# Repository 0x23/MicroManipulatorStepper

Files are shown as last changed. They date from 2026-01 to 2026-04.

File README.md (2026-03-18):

# Open Micro-Manipulator

This project contains an open source low-cost, easy-to-build motorized **XYZ Micro-Manipulator** motion control platform achieving submicron precision.
It's designed for applications such as optical alignment, probing electronic components, and microscopy.

Check out the YouTube video for more information about the device and how it is built:<br>
[An Open Source Motorized XYZ Micro-Manipulator - Affordable sub µm Motion Control](https://youtu.be/MgQbPdiuUTw)

<div style="display: flex; gap: 2%;">
  
  
</div>

Thanks to its parallel kinematic structure and miniature ball joints, it achieves good mechanical stiffness and a large range of motion.
The motors are off the shelf stepper motors driven by a 30 kHz closed loop controller and a very precise PWM signal.
A 'magnetic gearing' approach increases the resolution of the low-cost magnetic rotary encoders by a factor of 30 allowing for steps down to 50nm
(**Please mind the difference between resolution and accuracy**. The absolute accuracy is significantly worse.

The device can be controlled via simple G-Code commands over a USB serial interface and is thus easily integrated into other projects.
The firmware implements a complete motion planning stack with look-ahead for smooth and accurate path following capabilities.

## Getting Started

Below is a list of high level steps you can follow if you want to replicate the project. 
If you have questions or problems with the build or just want to discuss subjects related to the project, 
joint the projects community [Discord Server](https://discord.gg/maRvMVpa2Q).

1. Read this Document and watch the linked videos
2. Get the parts listed in [Bill of Materials](documentation/bom/bom.md)
3. Build the device and electronics
4. Change the hardware configuration according to your build [hw_config.h](firmware/MotionControllerRP/src/hw_config.h)
5. Upload firmware using VSCode with PlattformIO plugin
6. Calibrate axis

Also check out the setup guide for new devices: [Setup Guide](documentation/setup_guide/setup_guide.md)

## ✨NEW: Hardware Version 4.0
A new version of the hardware has been released, fixing several issues with the previous design:

- Self collision during homing fixed.
- Connection of ball joint block with screws only was not well constrained and could rotated a bit.
- No reliable way to ensure consistent linkage rod length
- Unnecessary ball joint friction
- Accurate ball position heavily dependet on print quality and corner rounding
- Rubber bands could not be changed or removed once glued in.

A video about the improved ball joint and linkage manufactoring process can be found on YouTube: [Better Ball Joints for the Open Micro-Manipulator](https://www.youtube.com/watch?v=NM2KXvRGmpg)
Also the FreeCAD model was restructured and improved and now includes all pins and fasteners. It now provides a reference for all required mechanical parts. 

<div style="display: flex;">
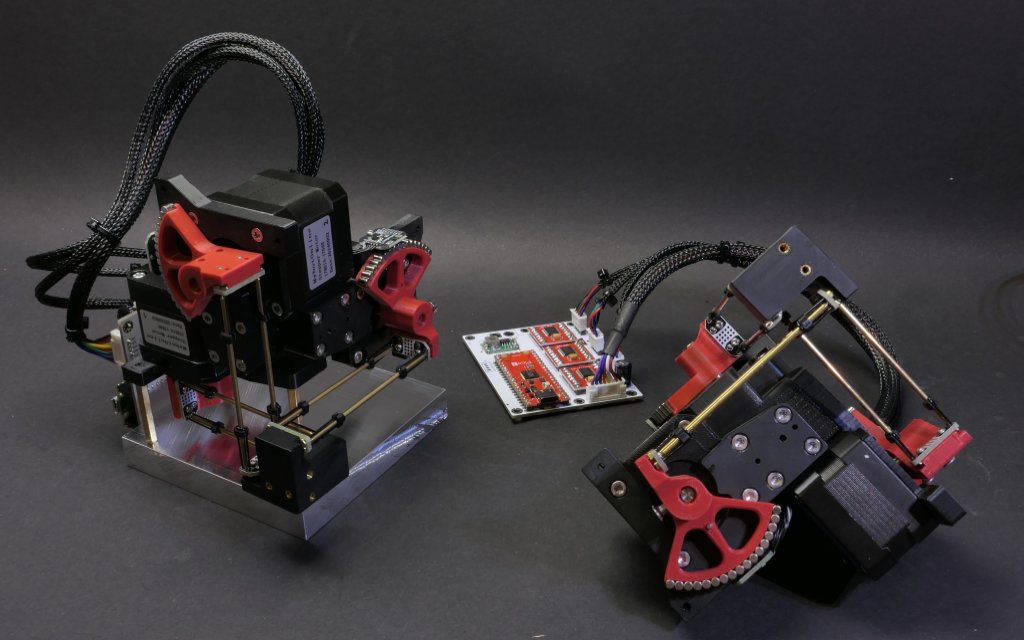
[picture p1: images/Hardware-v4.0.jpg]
    
</div>

WARNING: BOM is not updated yet...

## Open Micro-Manipulator GUI
To make testing and using the Open-Micro Manipulator easy and convenient a python control program with a graphical user interface is provided here: [Open Micro-Manipulator GUI](https://github.com/0x23/OpenMicroManipulatorGUI).
It has simple controlls to move the device around, while also displaying a live camera feed (e.g. from a microscope camera). Additional features, include a simple g-code runner and realtime mouse control (e.g. for Biology applications).

<div style="display: flex;">
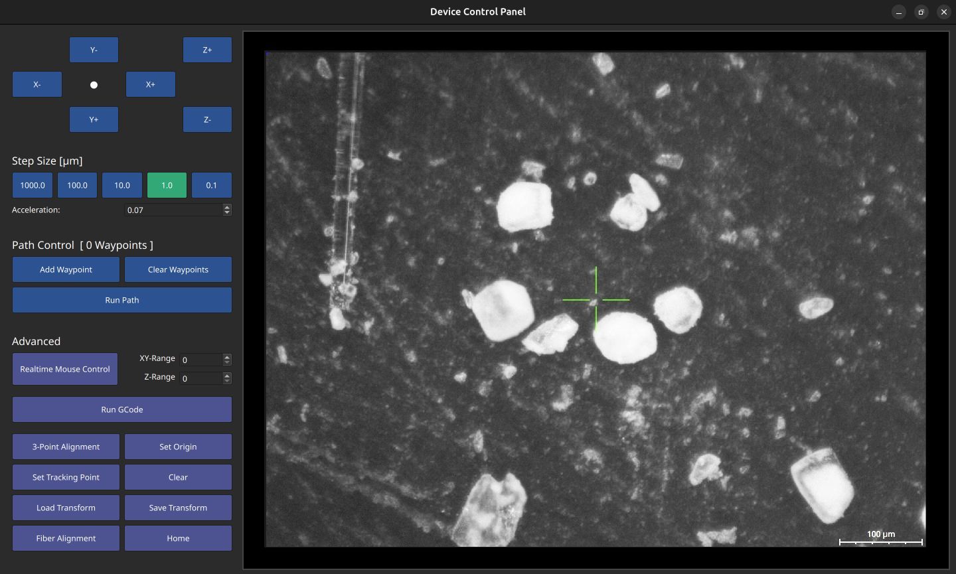
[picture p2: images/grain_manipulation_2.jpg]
    
</div>

## 🐍 Python-API

The lightweight Python API handles all serial communication and provides convenient command execution and debug message printing.
The interface includes functions to home, move, and calibrate the device, as well as to query device information.
Simply copy the [open_micro_stage_api.py](software/PythonAPI/open_micro_stage_api.py) file into your project (also install the dependencies in requirements.txt), and you’re ready to get started.

## Usage Example
```python
from open_micro_stage_api import OpenMicroStageInterface

# create interface and connect
oms = OpenMicroStageInterface(show_communication=True, show_log_messages=True)
oms.connect('/dev/ttyACM0')

# run this once to calibrate joints
# for i in range(3): oms.calibrate_joint(i, save_result=True)

# home device
oms.home()

# move to several x,y,z positions [mm]
oms.move_to(0.0, 0.0, 0.0, f=10)
oms.move_to(3.1, 4.1, 5.9, f=26)
oms.move_to(0.0001, 0.0, 0.0, f=10)

# wait for moves to finish
oms.wait_for_stop()
```

## API Functions (most relevant functions only)
```python
connect(port, baud_rate=921600)
disconnect()
set_workspace_transform(transform)
get_workspace_transform()
home(axis_list=None)
calibrate_joint(joint_index, save_result)
move_to(x, y, z, f, move_immediately, blocking, timeout)
set_tool_output(tool_idx, output_value, immediate)
set_pose(x, y, z)
dwell(time_s, blocking, timeout)
enable_motors(enable)
wait_for_stop(polling_interval_ms, disable_callbacks)
set_max_acceleration(linear_accel, angular_accel)
set_servo_parameter(pos_kp, pos_ki, vel_kp, vel_ki, vel_filter_tc)
```
## ✨ Firmware v1.0.4

Firmware 1.0.4 comes with many smaller improvements and bugfixes and a great new feature as well:

 - **Tools**: Tool usage (for example for laser engraving) is now supported on the two GPIO pins of J5 on the pcb.
              Tools are integrated into the planner and run fast and with correct timing when executing g-code.
              The tools support PWM (using the PIO feature to squeeze out extra channels without relying on software PWM).

   Example usage:
   ```
     M3 T0 S0.7  // set pwm output of tool 0 to 70%
     G4 S0.001   // dwell command (or any other motion command) - necessary to apply the tools output
   ```
   
- **Calibration**: Calibration has now some addition error checks to improve error reporting of potential problems like encoder alignment.
- **Kinematic Model Parameter**: Initialization code has been cleaned up and better comments where added to the parameters. Parameters are preset for HW v4.0 but you can toggle back to the old HW-v3.0 parameters if necessary.
- **Bugfixes**: smaller bugfixes

IMPORTANT: If you have **Hardware Version v3.0** you need to switch back to the old kinematic parameters in the [kinematic_model_delta3d.cpp](firmware/MotionControllerRP/src/kinematic_models/kinematic_model_delta3d.cpp) file (there is an #define for that at the top).

## Firmware v1.0.1

This update improves calibration, homing, logging, and adds several new G-Code commands.

### Improvements
- **Homing**: parallel homing support, higher repeatability, more accurate geometric reference  
- **Joint calibration**: refined procedure, persistent flash storage (no recalibration after reboot)  
- **Logging**: clearer and more detailed output  

### New G-Code Commands
- `G28` — Home joints (supports homing multiple axis simultanously for faster startup)
- `G24` — Set pose command (directly sets servo targets, bypassing motion controller)  
- `M17/M18` — Enable/Disable motors (with pose recovery from encoders on enable)  
- `M51` — Read encoder values  
- `M55` — Set servo loop parameters 
- `M56` — Joint calibration (with save-to-flash option)  
- `M57` — Read various information about the device state  
- `M58` — Read firmware version

## ⚙ CAD-Files

All CAD models are made in **FreeCAD** to allow everyone to view and modify the design without subscribing or paying for a proprietary CAD solution.
Note that most components are already designed with the goal to make them easily machinable on a 3-Axis CNC-Mill.
You can also 3D-Print the parts but have to live with thermal drift (carbon filled filaments can reduce this problem).

<div style="display: flex;">
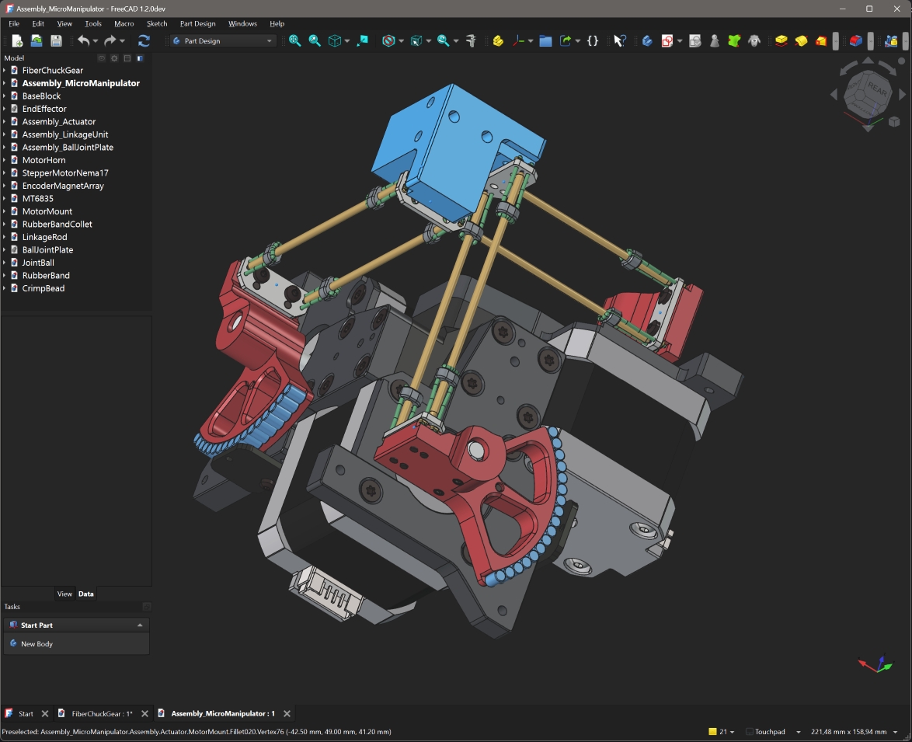
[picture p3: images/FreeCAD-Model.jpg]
FreeCAD Model
    
</div>

<br>

The CAD files can be found here: [CAD Models](construction).
Please note that FreeCAD version **1.2.0dev** was used, and the files might not work with older versions.

STL files for printing can be found here: [STL Files](construction/STL_3D_Printing/)

## ⚙ Kinematic Model

The kinematic model is defined here: [kinematic_model_delta3d.cpp](firmware/MotionControllerRP/src/kinemtaic_models/kinematic_model_delta3d.cpp).
Please check the dimensions of your build against the values set in the constructor. In particular, make sure the arm length matches.

## ⚙ Electronics

IMPORTANT: If you fabricated PCB version v1.2 (see version label on the board) you need to drill out a misplaced via on diode D1 that shorts 5V rail to ground (See [repair image](electronics/pcb_v1.2_fix.jpg) ). The problem was fixed in v1.3.

The electronics are designed in **KiCAD** and only commonly available modules (motor drivers and MCU boards) are used and connected by a simple PCB. No SMD soldering is required to populate the board to make the build extra accessible.
For usual winding resistance of your motors, the device should be powered by $${\color{lightgreen} 5V-6V }$$ (2A) to keep current and heating to a reasonable level.

<div style="display: flex; gap: 5%;">
  
  
</div>

The repository now also contains the fabrication files that can be directly uploaded to the PCB manufacturer.

## ⚙ Firmware

The firmware is written in C++ and takes some inspiration from the 'SimpleFOC' project. It aims to be streamlined and readable without any extra fuss, focusing on the hardware used in this project.
It implements path planning with look-ahead and, unlike many other motion controller projects, supports true 6DOF-Pose interpolation and planning, making it ready for driving hexapod motion platforms; that may or may not be the next step for this project.

You may find configuration for pin numbers, motor type, and other parameters in [hw_config.h](firmware/MotionControllerRP/src/hw_config.h). Please check them before uploading the firmware.

<div style="display: flex; gap: 2%;">
  
  
</div>

### Building and Flashing the Firmware

For building and flashing the firmware, Visual Studio Code (available for free on Windows and Linux) is recommended.
Install the PlatformIO add-on and open the firmware folder. You can now build and flash the firmware like any other PlatformIO project.

## ⚙ G-Code Interface

The firmware supports only a small subset of G-Code commands listed below.  
Each command is acknowledged with either an **`ok`** or **`error`** response.  

If a command provides additional information (e.g., the *get position* command), that information is returned **before** the `ok` message.  
The client must wait for an acknowledgment from the previous command before sending the next one—otherwise, behavior is undefined.
| Command | Description |
|---|---|
| `G0 X Y Z F` | Move the end-effector in a straight line to the specified position. <br>• `X`, `Y`, `Z`: target positions <br>• `F`: feed rate |
| `G1 X Y Z F` | Same as `G0`. |
| `G4 S/P` | Dwell/pause for a specified time. <br>• `S`: seconds <br>• `P`: milliseconds |
| `G24 X Y Z A B C` | Directly set current pose for servo loops with optional rotation vector* `A`, `B`, `C`. |
| `G28 A-F` | Home one or more joints. <br>• Optional joint selection `A`–`F`. |
| `M3` | Set Tool output. <br>• `T`: tool index <br>• `S`: output value (0.0..1.0) <br> Note: new values is only applied on the next motion or dwell command |
| `M17` | Enable motors and read current pose as the start pose. |
| `M18` | Disable motors. |
| `M50` | Get current internal pose. (Encoders are not read here) |
| `M51` | Get current encoder angles (in degrees) and raw encoder values. |
| `M52` | Get the number of items in the planner queue. |
| `M53` | Check if all planned moves are finished (`1` = finished, `0` = not finished). |
| `M55 A B C D F` | Set servo loop parameters. <br>• `A`, `B`: position PI controller gains (P and I) <br>• `C`, `D`: velocity PI controller gains (P and I) <br>• `F`: velocity filter time constant |
| `M56 J S` | Calibrate a joint. <br>• `J`: joint index <br>• `S`: save calibration result |
| `M57` | Get device and servo loop info: homing/calibration state, angles, loop frequencies, and file list. |
| `M58` | Get firmware version. |
| `M204 L A` | Set linear and angular acceleration. <br>• `L`: linear acceleration <br>• `A`: angular acceleration |

*Note: The communication protocol uses 3D vectors for rotations. The direction represents the rotation axis and the length of the vector represents the angle of rotation around the axis.

## ❤️ Support

If you'd like to support this project, consider the following:

- **Contribute to the build guide** – Help improve or expand the build instructions by submitting pull requests or opening issues with suggestions.
- **Characterize typical radial stepper motor shaft error motion** – Measure radial error motion of the shaft of multiple Nema-17 stepper motors (see Cylos Garage for more information about the subject: https://www.youtube.com/watch?v=gt2gK-oxy5s).
- **Give feedback on the build experience** – Let us know what worked, what didn’t, and how the process could be smoother for others.
- **Support the project on Ko-fi** – If you find this project valuable, you can support it financially via [Ko-fi](https://ko-fi.com/diffractionlimited) ☕.

## Youtube Video
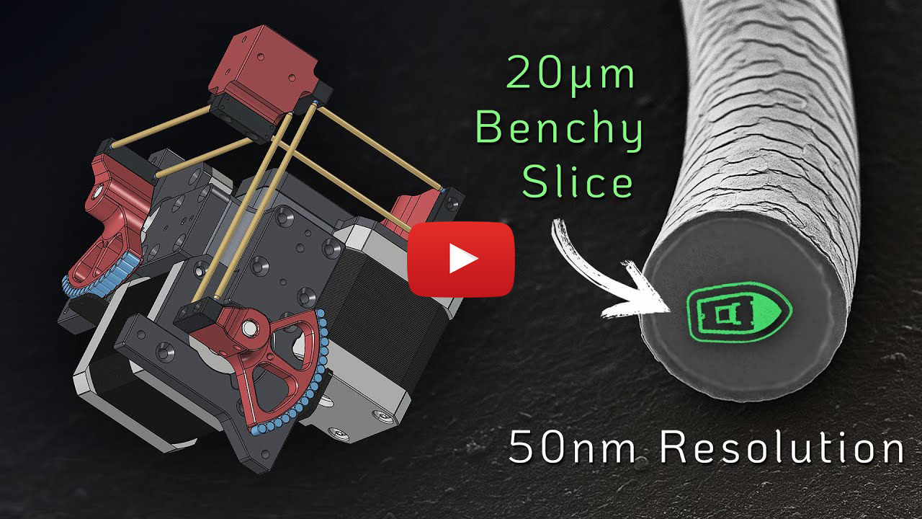
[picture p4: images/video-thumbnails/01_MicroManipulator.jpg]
Watch the video (https://youtu.be/MgQbPdiuUTw)

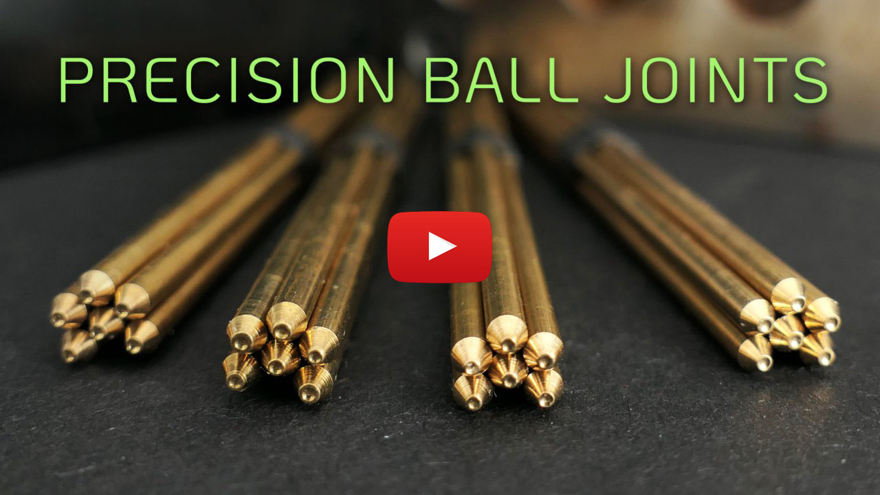
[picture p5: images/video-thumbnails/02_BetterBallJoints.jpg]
Better Ball Joints for the Open Micro-Manipulator (https://youtu.be/MgQbPdiuUTw)


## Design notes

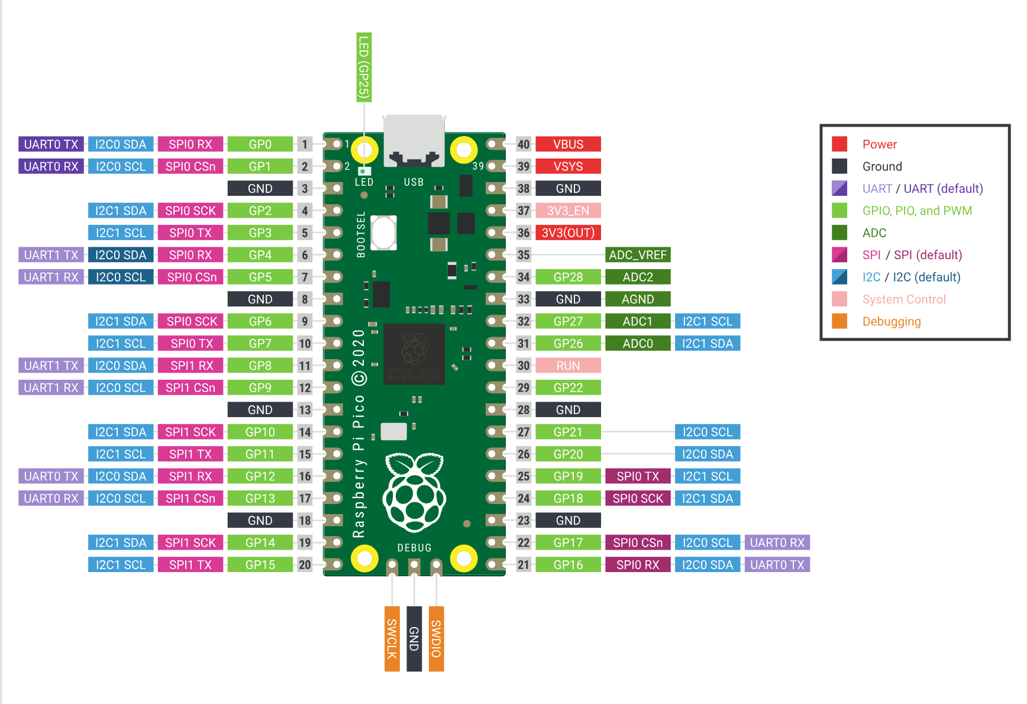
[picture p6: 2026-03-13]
firmware/MotionControllerRP/Rp2350-Pico_Pinout.png

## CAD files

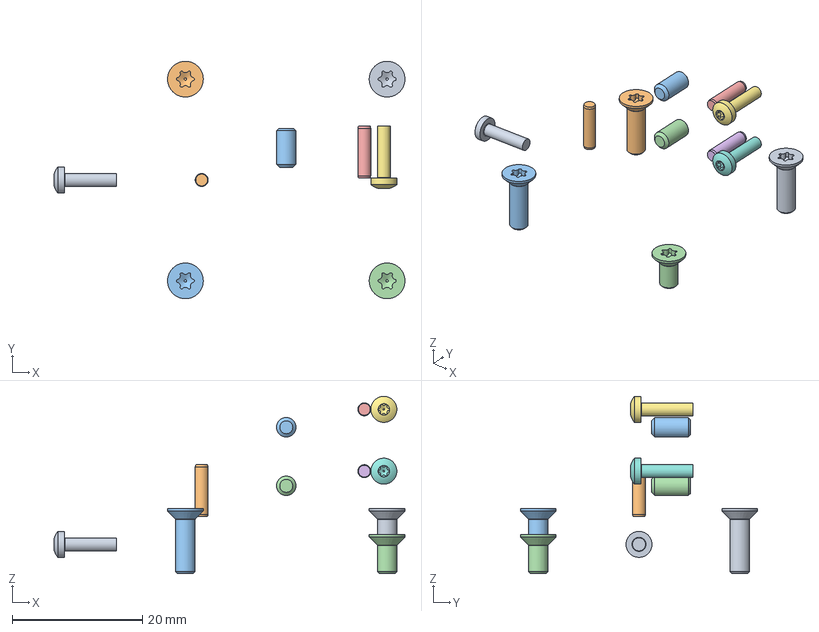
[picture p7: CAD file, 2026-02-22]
construction/micro_manipulator/Assembly_Actuator.FCStd
53.9 x 36.5 x 27.2 mm
M3x10-Screw x 2
M3x10-Screw008 x 2
M3x10-Screw009 x 2
M3x6-Screw x 2
2 mmx8-Pin x 2
2 mmx8-Pin012 x 2
M2x8-Screw x 2
M2x8-Screw009 x 2
M2x8-Screw004 x 2
2 mmx8-Pin011 x 2
M3x6-Screw003 x 2
M3x6-Screw004 x 2

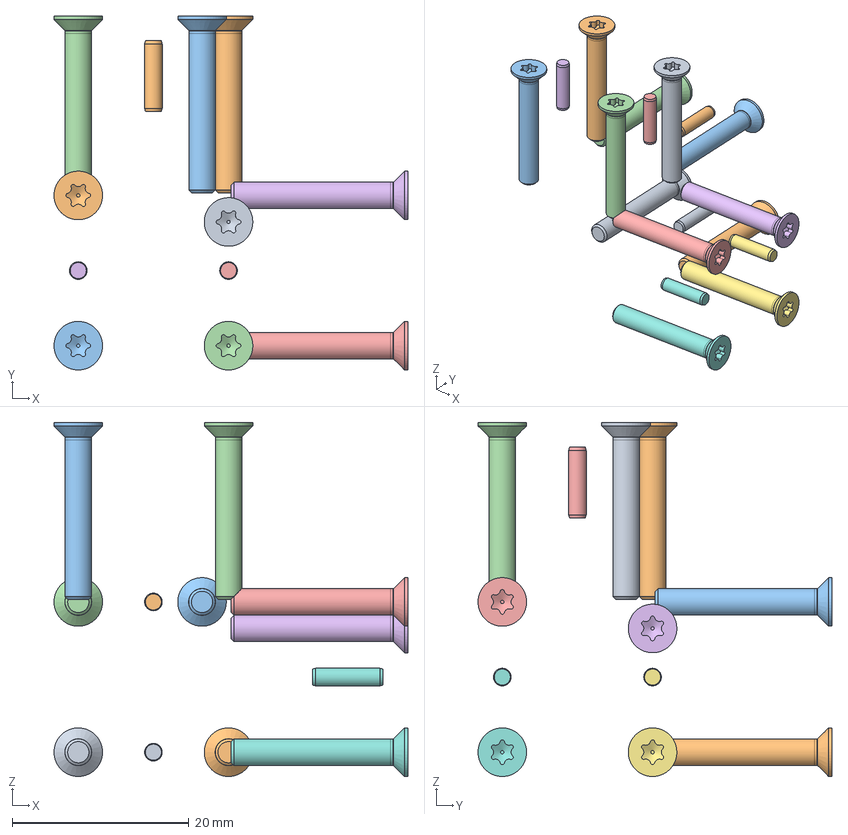
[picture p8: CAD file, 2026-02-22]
construction/micro_manipulator/Assembly_MicroManipulator.FCStd
40.0 x 40.0 x 40.0 mm
M3x20-Screw x 2
M3x20-Screw281 x 2
M3x20-Screw282 x 2
M3x20-Screw283 x 2
M3x20-Screw277 x 2
M3x20-Screw278 x 2
M3x20-Screw279 x 2
M3x20-Screw280 x 2
M3x20-Screw262 x 2
M3x20-Screw263 x 2
M3x20-Screw264 x 2
M3x20-Screw265 x 2
2 mmx8-Pin027 x 2
2 mmx8-Pin028 x 2
2 mmx8-Pin029 x 2
2 mmx8-Pin030 x 2
2 mmx8-Pin031 x 2
2 mmx8-Pin032 x 2

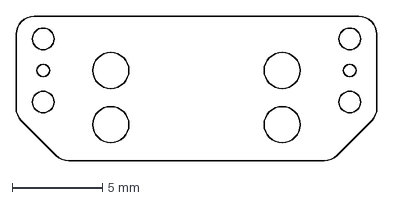
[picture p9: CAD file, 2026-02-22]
construction/micro_manipulator/balljoint_plate_pcb/BallJointPlate-Contour.dxf
20.0 x 8.00 mm

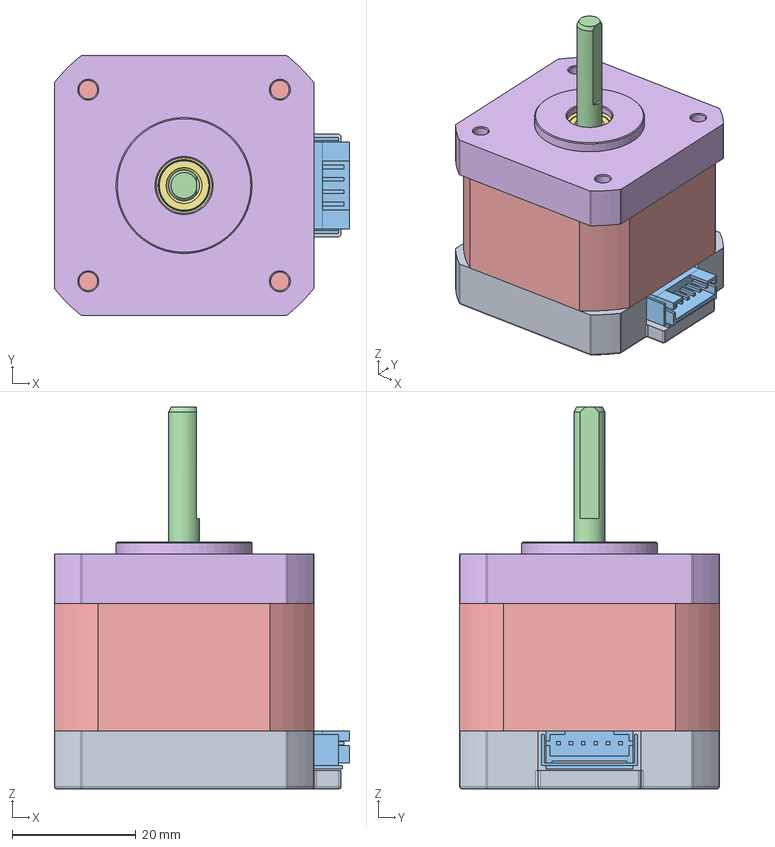
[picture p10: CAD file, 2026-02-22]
construction/micro_manipulator/StepperMotorNema17.FCStd
47.8 x 42.0 x 61.8 mm
rear end cap
rear bearing
connector
shaft
stator
front end cap
front bearing
M3x10-Screw
M3x10-Screw004
M3x10-Screw005
M3x10-Screw006

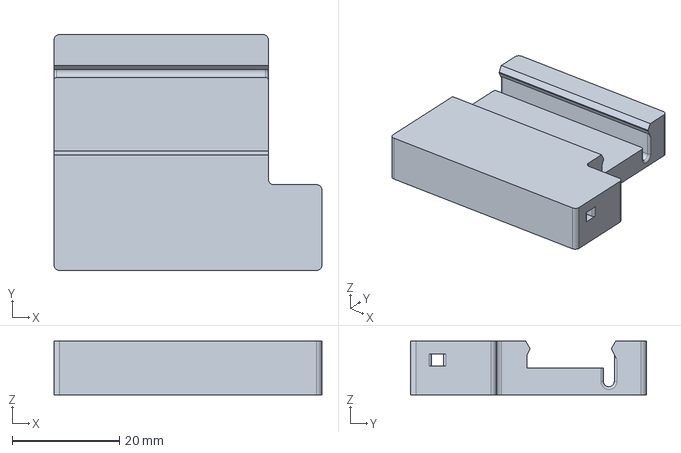
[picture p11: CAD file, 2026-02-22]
construction/tools/rod_embossing_tools/rod_lenth_setting_press/rod_guide.FCStd
50.0 x 44.0 x 10.0 mm

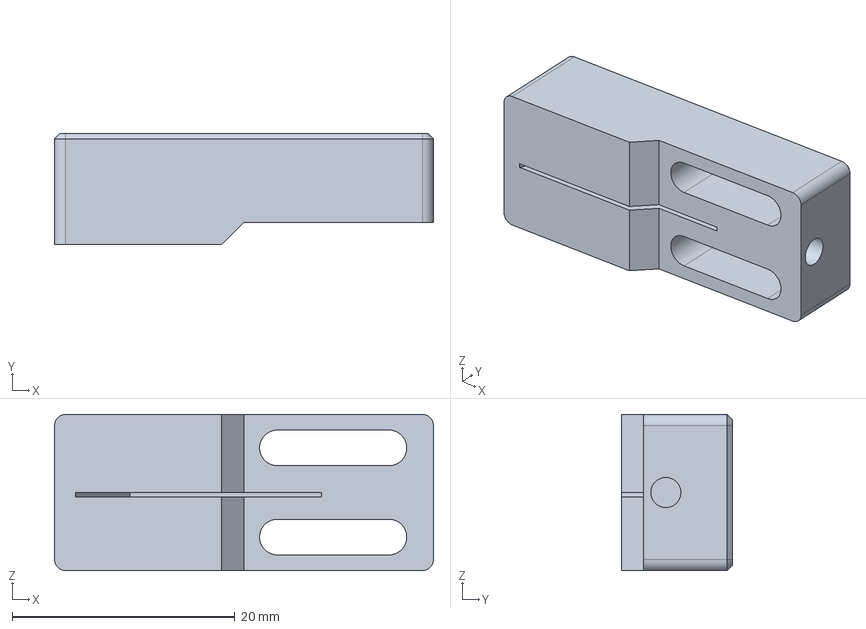
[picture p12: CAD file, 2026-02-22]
construction/tools/rod_embossing_tools/rod_sharper/BladeCarrier.FCStd
34.0 x 10.0 x 14.0 mm

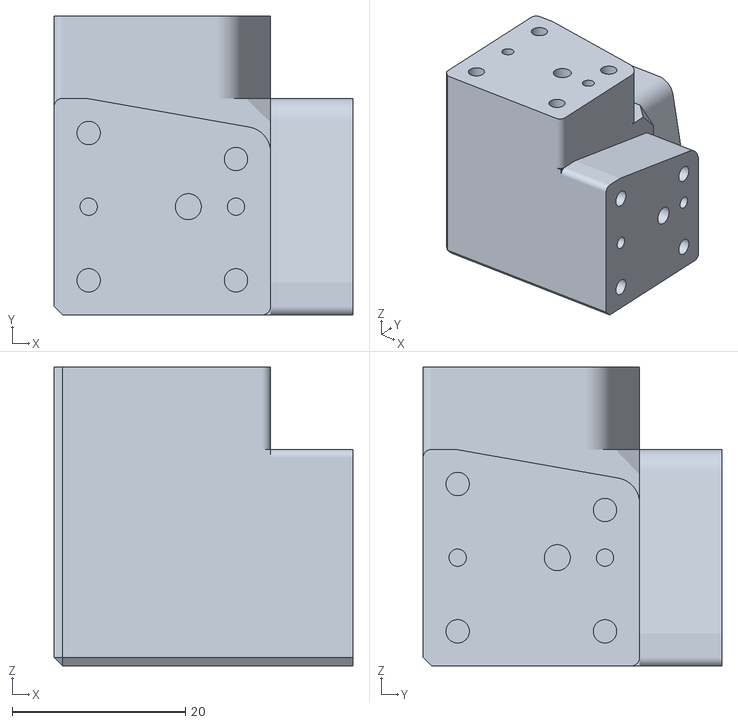
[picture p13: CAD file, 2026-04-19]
construction/v4_3dprinting_stl/machine/BaseBlock.stl
34.5 x 34.5 x 34.5

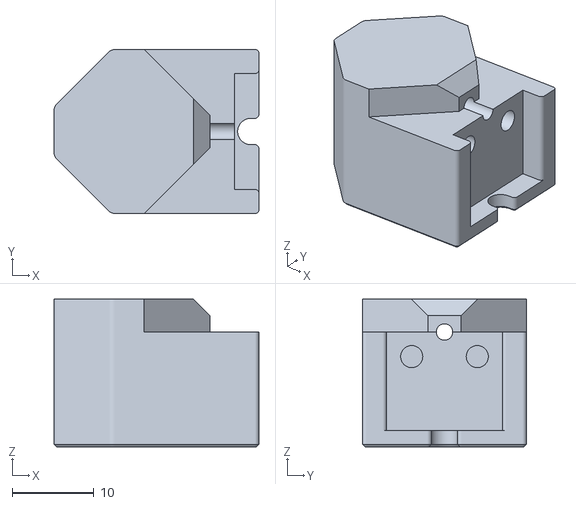
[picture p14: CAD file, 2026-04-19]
construction/v4_3dprinting_stl/tools/rod_sharpener/RodGuide.stl
25.0 x 20.0 x 18.0

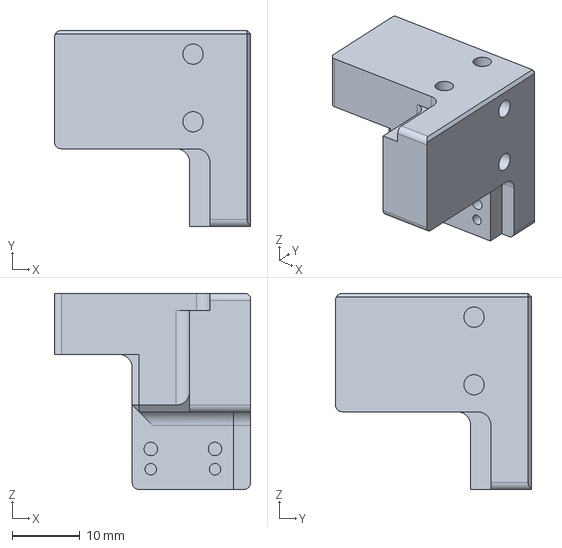
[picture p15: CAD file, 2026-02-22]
construction/micro_manipulator/EndEffector.FCStd
29.0 x 29.0 x 29.0 mm

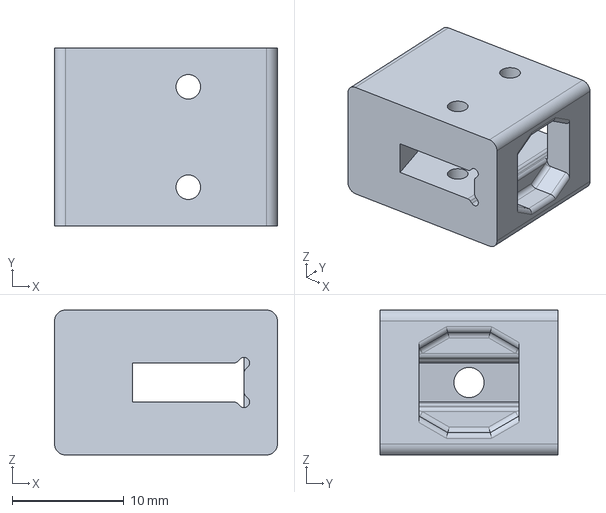
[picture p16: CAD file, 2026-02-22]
construction/tools/rod_embossing_tools/rod_lenth_setting_press/caliper_clamp.FCStd
20.0 x 16.0 x 13.0 mm

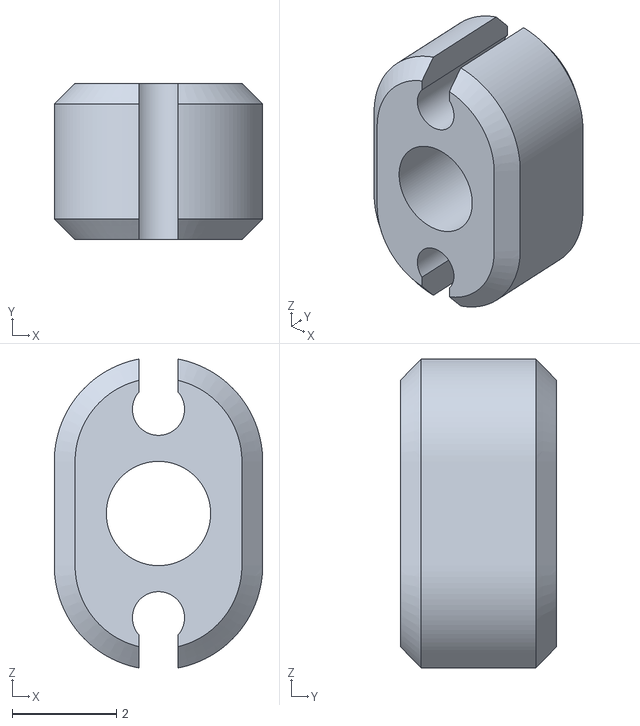
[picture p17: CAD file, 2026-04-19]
construction/v4_3dprinting_stl/machine/RubberBandCollet.stl
4.00 x 3.00 x 5.93

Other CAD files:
construction/micro_manipulator/Assembly_EndEffector.FCStd
construction/micro_manipulator/Assembly_BallJointPlate.FCStd
construction/micro_manipulator/Assembly_LinkageUnit.FCStd
construction/v4_3dprinting_stl/tools/rod_length_setting_press/RodGuide.stl
construction/tools/rod_embossing_tools/rod_sharper/RodGuide.FCStd
construction/v4_3dprinting_stl/tools/rod_length_setting_press/CaliperClamp.stl
construction/v4_3dprinting_stl/tools/rod_sharpener/BladeCarrier.stl
construction/micro_manipulator/BallJointPlate.FCStd
construction/micro_manipulator/BaseBlock.FCStd
construction/micro_manipulator/CrimpBead.FCStd
construction/micro_manipulator/EncoderMagnet.FCStd
construction/micro_manipulator/EncoderMagnetArray.FCStd
construction/micro_manipulator/JointBall.FCStd
construction/micro_manipulator/LinkageRod.FCStd
construction/micro_manipulator/MT6835.FCStd
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

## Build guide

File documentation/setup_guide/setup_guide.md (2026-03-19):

# Setup Guide

This guide walks you through the setup of your new **Open Micro-Manipulator** device.

## Checklist for New Devices

1. **Was the mechanical limit pin added to the rotor?**  
   This pin is required for proper homing of the device.

    <div style="display: flex;">
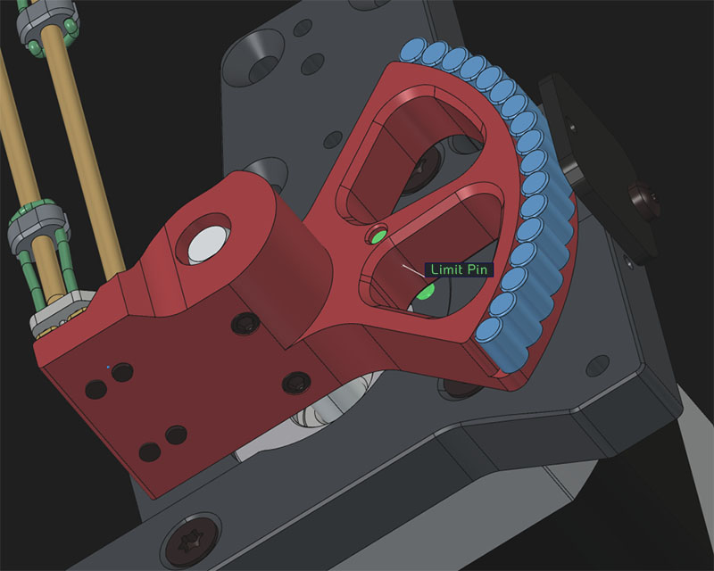
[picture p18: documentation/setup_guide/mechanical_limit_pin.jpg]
Mechanical Limit Pin
        
    </div>

2. **Are the screws that secure the rotor to the motor shaft installed?**  
   If the rotor is not firmly attached, it may slip imperceptibly during homing or other movements, leading to problems during calibration and homing.

3. **Is the homing direction correct?**  
   During the homing command (`G28`), the end effector should move toward the base.  
   If it moves in the opposite direction, rewire the motor to reverse its direction.

   <div style="display: flex;">
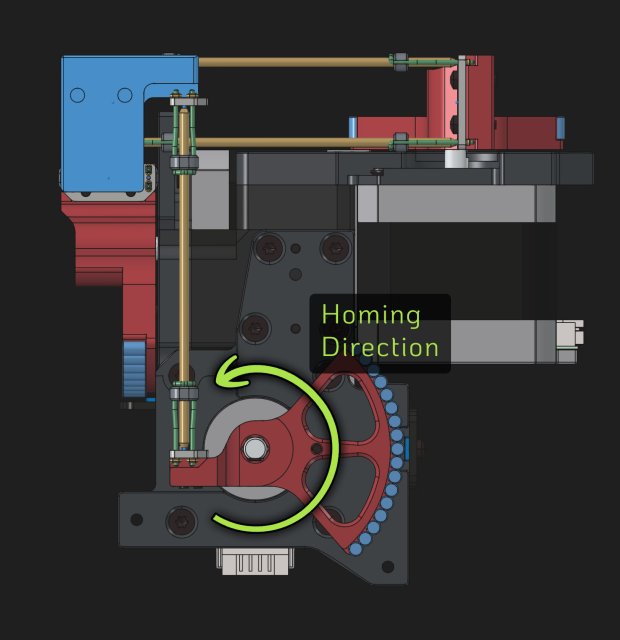
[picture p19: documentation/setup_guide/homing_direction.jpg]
       
   </div>

## Calibration and Checking the Encoders

You can use the calibration plotter to check if your encoders are working as expected.
On the left you see a good calibration on the right a bad calibration.

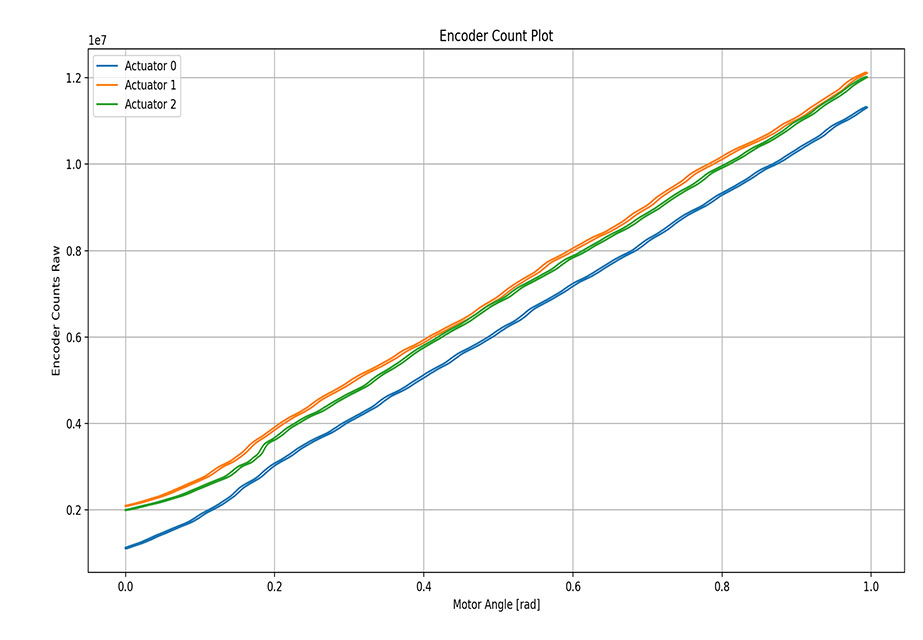
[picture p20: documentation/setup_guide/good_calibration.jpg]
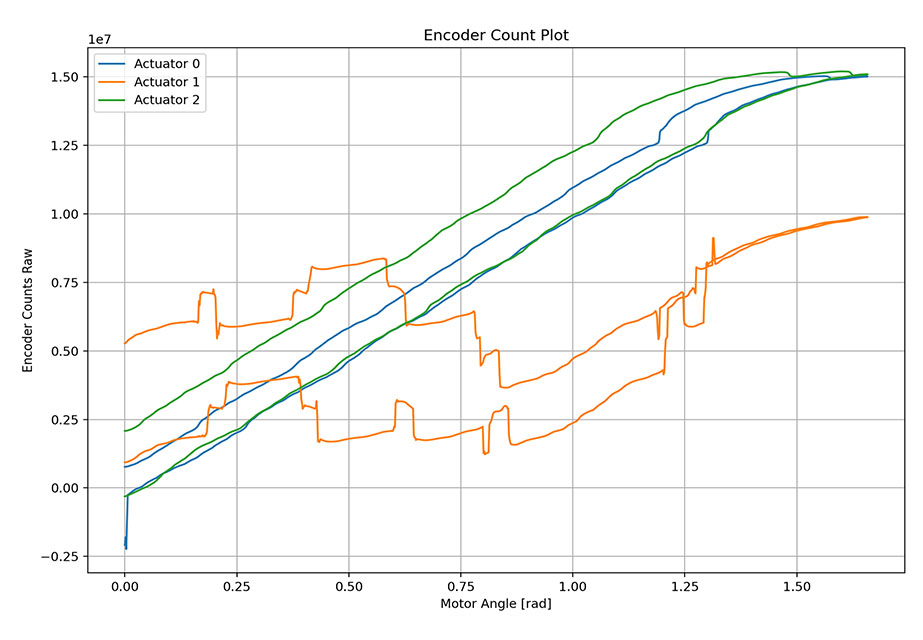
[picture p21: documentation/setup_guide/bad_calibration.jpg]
|  |  |
:--:|:--:
| **Good calibration** | **Bad calibration** |

THIS DOCUMENT IS UNFINISHED AND WORK IN PROGRESS...

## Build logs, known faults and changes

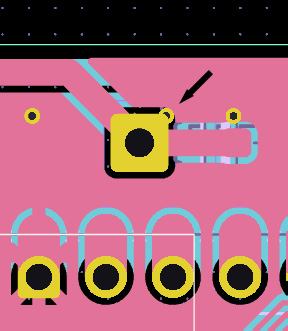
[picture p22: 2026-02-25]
electronics/control_board/pcb_v1.2_fix.jpg

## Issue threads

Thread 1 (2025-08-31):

Link the YouTube video in the README

gdevenyi, 2025-08-31:
Currently it's missing

https://youtu.be/MgQbPdiuUTw

Closed 2025-09-01.

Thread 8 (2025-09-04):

Questions about BOM file (Encoder qty, steel ball size, stepper motor spec)

Jonas-Meyer97, 2025-09-04:
Hello,

I have a few questions regarding the BOM file:

- The MT6835 Magnetic Encoder Module is listed with a quantity of 4, but from the design it seems only 3 are required. Could you confirm the correct number?
- The steel ball is noted as 1.25 mm diameter, but the CAD files and video reference 1.5 mm. Which size should be used?
- For the Nema 17 stepper motor, should we use the 1.8° or 0.9° variant?

Thanks for clarifying!

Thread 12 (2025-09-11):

Short to GND on diode output.

Dainius-G, 2025-09-11:
Short to GND on diode output.

0x23, 2025-09-13:
PCB layout is corrected.

Closed 2025-09-13.

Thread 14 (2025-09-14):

chore(electronics): add .gitignore

gustavo-alberto, 2025-09-14:
### Description
The `electronics` module currently does not have a `.gitignore` file.
This causes unnecessary temporary files to be tracked in version control.

### Proposed solution
- Add a `.gitignore` file to the `electronics` module.

### Benefits
- Keeps the repository clean.
- Prevents accidental commits of temporary files.
- Improves collaboration by reducing noise in pull requests.

Closed 2025-09-14.

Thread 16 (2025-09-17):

Assembly instructions / WireMountfixture ?

11mbs, 2025-09-17:
Hi,
Thank you so much for the amazing project!
It's so beautifully designed and I'm really excited to build one. :D

Just before  all the parts have arrived, I was looking around and came up with a few questions about assembly:
1. Is there any use for the Wire Mount Fixture model, or is it left over from the previous project / versions?

2. How long to make the loops of the PU rubber band?
The video shows 50mm lengths being cut, but the length of the loop doesn't match this after trimming.

3. I notice the BOM here says 1.25mm steel balls, but the video says 1.5mm - are both usable?

Thanks again for all the work you've put in here, it's really really cool!

JamesNewton, 2025-09-17:
Jumping in to help where I can. Your question 3 has been answered before: The size isn't critical.

0x23, 2025-09-18:
1. Its a leftover and I removed it from the repo, thanks for pointing that out
2. The total length of rubberband in the loop (not counting the length within the holes)  is about 20mm
3. Both work - I will probably go down to 1mm in future with the upcoming ball joint improvement
4. I use a pressfit and it works so far (but not ideal with 3d-printed parts). I recommend a drop of CA-Glue
5. Yes (CA-Gue as well). I plan to use screws in future but I am not there yet with the design.
6. There are three mounting 3 holes in the motor plate. I temporary mounted my device with 3d printed spacers to a steel plate:

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

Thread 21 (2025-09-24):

FreeCAD blog post and FOSDEM

concretedog, 2025-09-24:
Hi, I'm Jo and I write some content for the official FreeCAD news blog and I've just drafted a post on this amazing project. It's probably scheduled for publishing tomorrow or Friday. I'm just wondering though were you are in the world and if by any chance you were planning to attend FOSDEM next year? FreeCAD and KiCad have a joint booth each year and this would be an amazing project to have on the booth desk showcasing both FreeCAD and KiCad. Obviously unlikely this can happen, but it's always worth asking!

concretedog, 2025-09-25:
The post is now live on the [FreeCAD blog](https://blog.freecad.org/2025/09/25/forged-in-freecad-xyz-micro-manipulator-for-sub-micron-motion-control/).

0x23, 2025-09-26:
FOSDEM is in Brussels right? Its actually not too far away. Can you contact me via email ?

concretedog, 2025-09-26:
Yes Brussels, 31st January 1st Feb 2026. https://fosdem.org/2026/

concretedog, 2025-09-26:
Just emailed you on the email in your recent commits. Maybe check spam etc. Be great if we can work this out!

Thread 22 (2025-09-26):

Discord

Dainius-G, 2025-09-26:
Hi

Thank you for sharing such an interesting project! I’m currently in the middle of building the MicroManipulatorStepper and really enjoying it.

From what I’ve seen, most of the project’s presence is on YouTube and GitHub. Those are great for publishing updates and source code, but they don’t provide an easy space for builders to discuss, debug, and customize the project together.

Would you be interested if I set up a simple Discord server dedicated to this project? It could give the community a place to collaborate, share builds, and support each other.

0x23, 2025-09-27:
Not sure how much time I am able to find hanging around but as you mentioned it can be a great place for others to exchange ideas and help each other. If you set up a server for the project would you be willing to transfer ownership of the server in the future?

Dainius-G, 2025-09-28:
https://discord.gg/km6RvSvX

0x23, 2025-09-29:
Perfect ! I added the link to the main page.

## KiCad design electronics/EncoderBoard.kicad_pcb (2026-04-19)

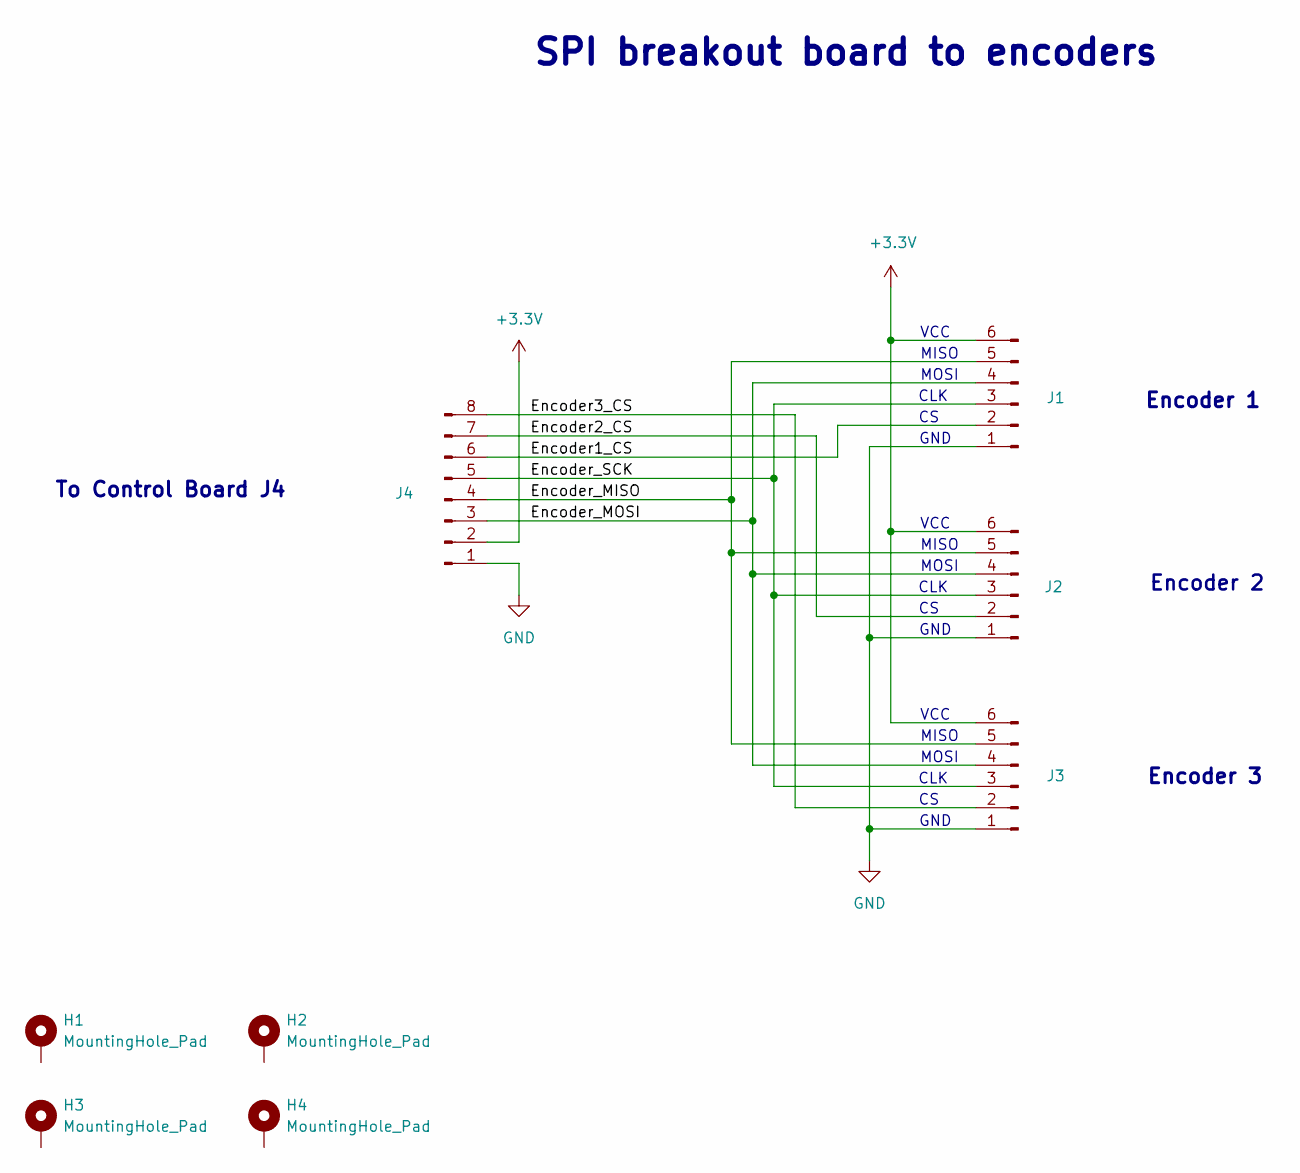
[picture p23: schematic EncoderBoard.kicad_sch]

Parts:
H1, H2, H3, H4: MountingHole_Pad; MountingHole_2.7mm_M2.5_Pad_Via
J1, J2, J3: Conn_01x06_Pin; JST_PH_B6B-PH-K_1x06_P2.00mm_Vertical
J4: Conn_01x08_Pin; JST_PH_B8B-PH-K_1x08_P2.00mm_Vertical

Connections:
+3.3V: J1.6, J2.6, J3.6, J4.2
/Encoder1_CS: J1.2, J4.6
/Encoder2_CS: J2.2, J4.7
/Encoder3_CS: J3.2, J4.8
/Encoder_MISO: J1.5, J2.5, J3.5, J4.4
/Encoder_MOSI: J1.4, J2.4, J3.4, J4.3
/Encoder_SCK: J1.3, J2.3, J3.3, J4.5
GND: J1.1, J2.1, J3.1, J4.1

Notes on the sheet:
VCC
Encoder 2
CLK
MISO
To Control Board J4
MOSI
Encoder 3
SPI breakout board to encoders
GND
Encoder 1

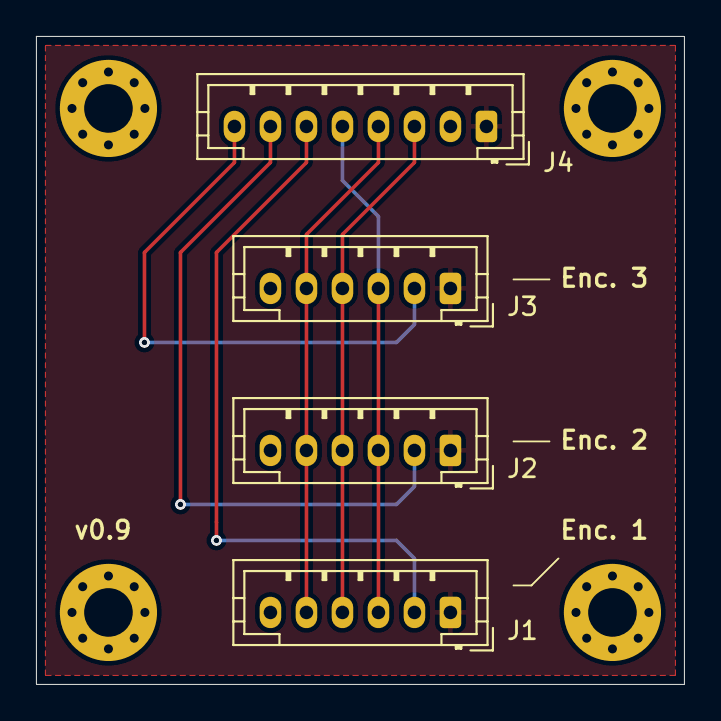
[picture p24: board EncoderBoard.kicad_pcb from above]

Board: 2 copper layers, 36.0 x 36.0 mm, 8 parts (0 on the bottom side), 8 nets.

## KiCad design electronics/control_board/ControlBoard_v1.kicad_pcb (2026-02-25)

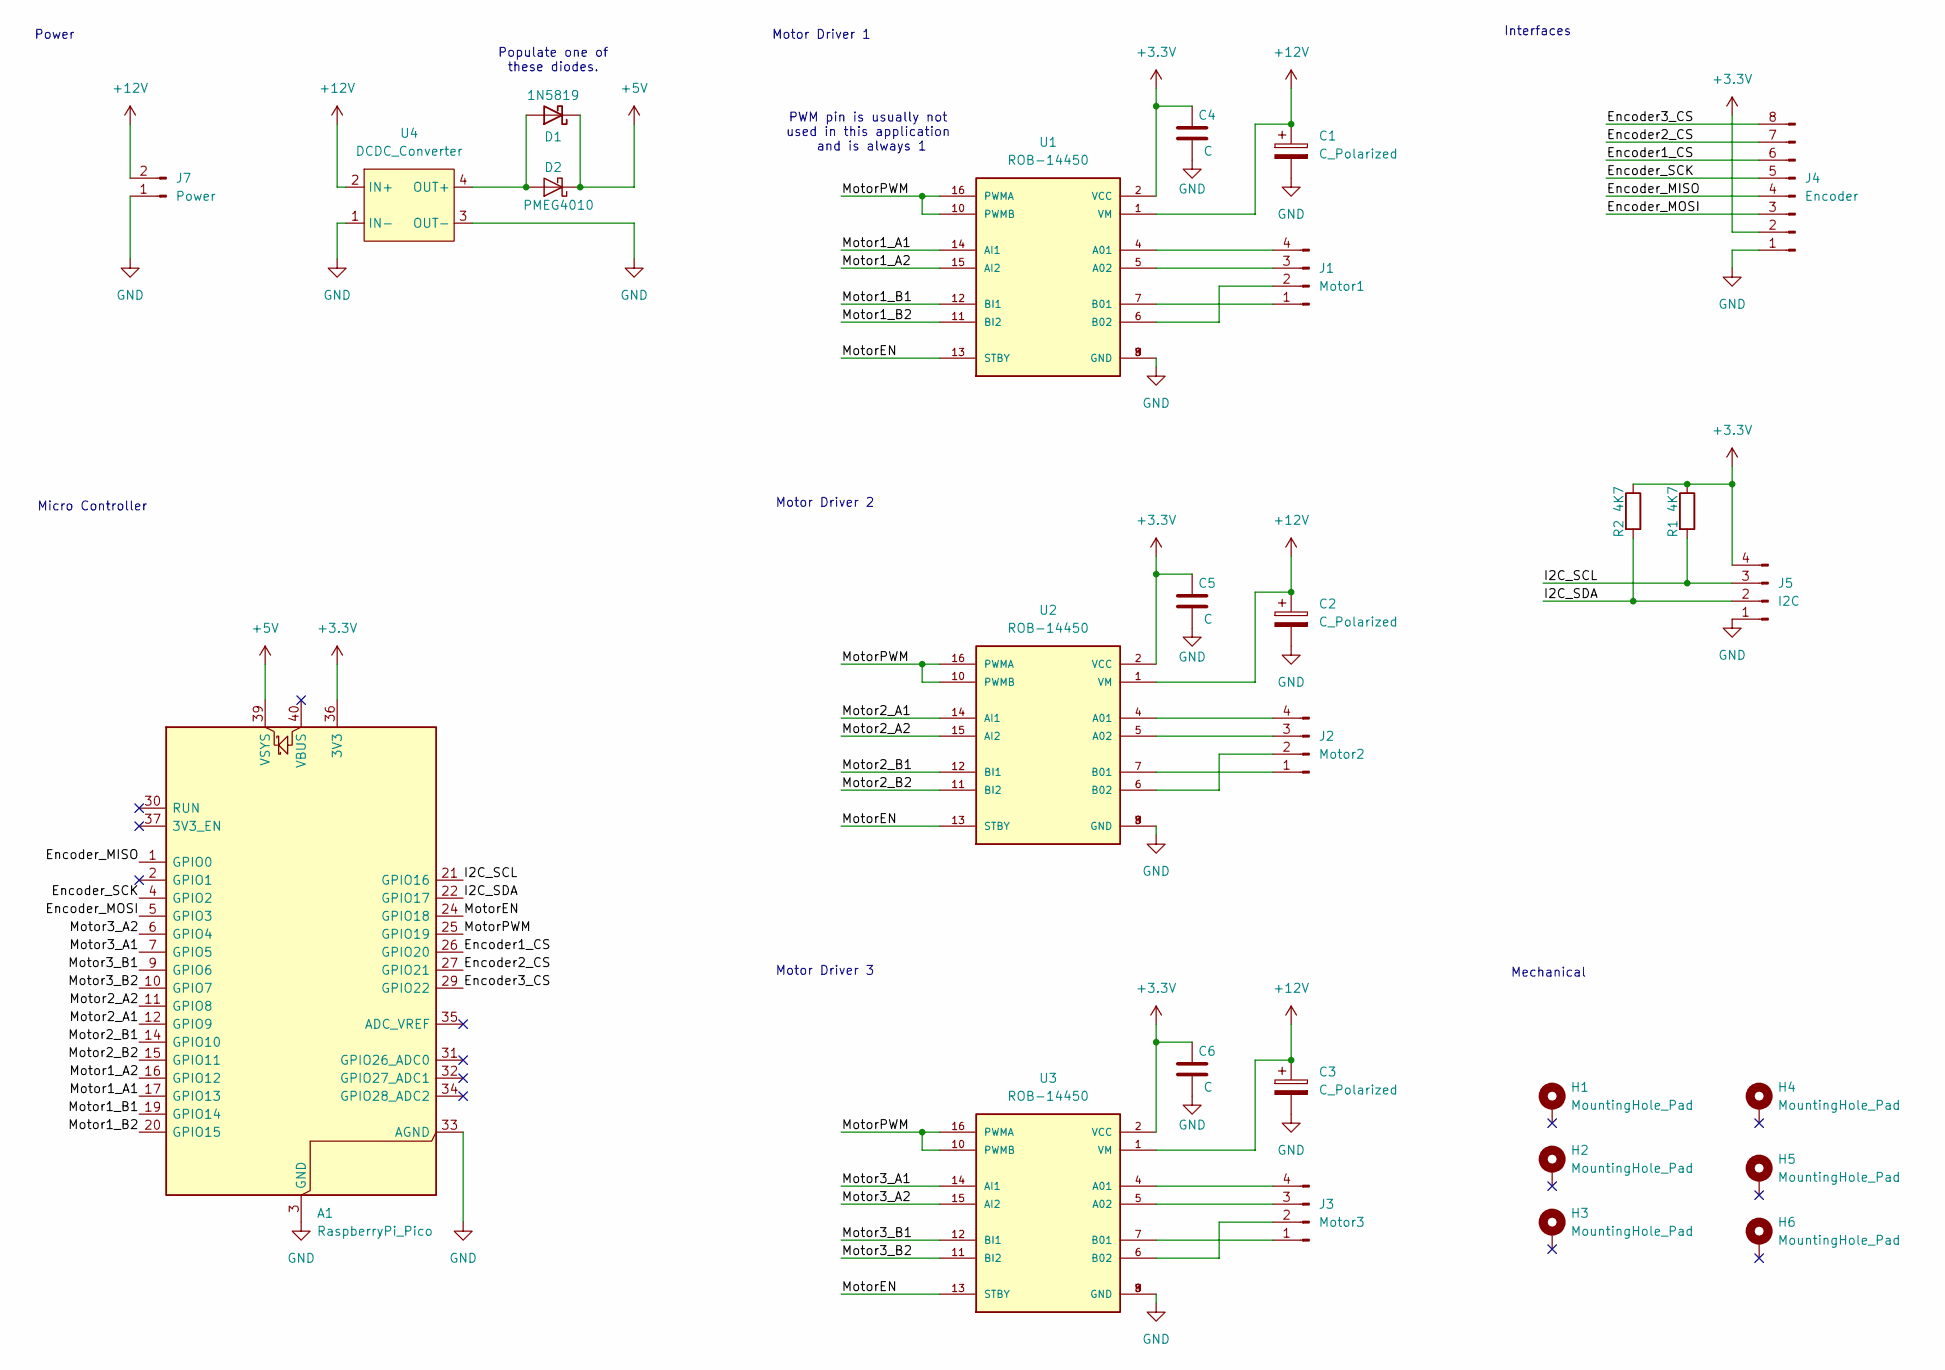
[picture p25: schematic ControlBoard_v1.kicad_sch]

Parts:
A1: RaspberryPi_Pico; RaspberryPi_Pico_Common_Unspecified
C1, C2, C3: C_Polarized; CP_Radial_D8.0mm_P3.50mm
C4, C5, C6: C; C_0603_1608Metric_Pad1.08x0.95mm_HandSolder
D1: 1N5819; D_DO-41_SOD81_P10.16mm_Horizontal
D2: PMEG4010; D_SOD-123F
H1, H2, H3, H4, H5, H6: MountingHole_Pad; MountingHole_2.7mm_M2.5_Pad_Via
J1: Motor1; PinHeader_1x04_P2.54mm_Vertical
J2: Motor2; PinHeader_1x04_P2.54mm_Vertical
J3: Motor3; PinHeader_1x04_P2.54mm_Vertical
J4: Encoder; JST_PH_B8B-PH-K_1x08_P2.00mm_Vertical
J5: I2C; JST_PH_B4B-PH-K_1x04_P2.00mm_Vertical
J7: Power; AMASS_XT60-M_1x02_P7.20mm_Vertical
R1, R2: 4K7; R_0603_1608Metric_Pad0.98x0.95mm_HandSolder
U1, U2, U3: ROB-14450; MODULE_ROB-14450; PARTREV 11-13-17
U4: DCDC_Converter; DCDC_17mmx12mm

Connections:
+3.3V: A1.36 (3V3), C4.1, C5.1, C6.1, J4.2, J5.4, R1.1, R2.1, U1.2 (VCC), U2.2 (VCC), U3.2 (VCC)
+5V: A1.39 (VSYS), D1.1 (K), D2.1 (K)
+12V: C1.1, C2.1, C3.1, J7.2, U1.1 (VM), U2.1 (VM), U3.1 (VM), U4.2 (IN+)
/Encoder1_CS: A1.26 (GPIO20), J4.6
/Encoder2_CS: A1.27 (GPIO21), J4.7
/Encoder3_CS: A1.29 (GPIO22), J4.8
/Encoder_MISO: A1.1 (GPIO0), J4.4
/Encoder_MOSI: A1.5 (GPIO3), J4.3
/Encoder_SCK: A1.4 (GPIO2), J4.5
/I2C_SCL: A1.21 (GPIO16), J5.3, R1.2
/I2C_SDA: A1.22 (GPIO17), J5.2, R2.2
/Motor1_A1: A1.17 (GPIO13), U1.14 (AI1)
/Motor1_A2: A1.16 (GPIO12), U1.15 (AI2)
/Motor1_B1: A1.19 (GPIO14), U1.12 (BI1)
/Motor1_B2: A1.20 (GPIO15), U1.11 (BI2)
/Motor2_A1: A1.12 (GPIO9), U2.14 (AI1)
/Motor2_A2: A1.11 (GPIO8), U2.15 (AI2)
/Motor2_B1: A1.14 (GPIO10), U2.12 (BI1)
/Motor2_B2: A1.15 (GPIO11), U2.11 (BI2)
/Motor3_A1: A1.7 (GPIO5), U3.14 (AI1)
/Motor3_A2: A1.6 (GPIO4), U3.15 (AI2)
/Motor3_B1: A1.9 (GPIO6), U3.12 (BI1)
/Motor3_B2: A1.10 (GPIO7), U3.11 (BI2)
/MotorEN: A1.24 (GPIO18), U1.13 (STBY), U2.13 (STBY), U3.13 (STBY)
/MotorPWM: A1.25 (GPIO19), U1.10 (PWMB), U1.16 (PWMA), U2.10 (PWMB), U2.16 (PWMA), U3.10 (PWMB), U3.16 (PWMA)
GND: A1.3 (GND), A1.8 (GND), A1.13 (GND), A1.18 (GND), A1.23 (GND), A1.28 (GND), A1.33 (AGND), A1.38 (GND), C1.2, C2.2, C3.2, C4.2, C5.2, C6.2, J4.1, J5.1, J7.1, U1.3 (GND), U1.8 (GND), U1.9 (GND), U2.3 (GND), U2.8 (GND), U2.9 (GND), U3.3 (GND), U3.8 (GND), U3.9 (GND), U4.1 (IN-), U4.3 (OUT-)
unnamed: D1.2 (A), D2.2 (A), U4.4 (OUT+)
unnamed: J1.1, U1.7 (B01)
unnamed: J1.2, U1.6 (B02)
unnamed: J1.3, U1.5 (A02)
unnamed: J1.4, U1.4 (A01)
unnamed: J2.1, U2.7 (B01)
unnamed: J2.2, U2.6 (B02)
unnamed: J2.3, U2.5 (A02)
unnamed: J2.4, U2.4 (A01)
unnamed: J3.1, U3.7 (B01)
unnamed: J3.2, U3.6 (B02)
unnamed: J3.3, U3.5 (A02)
unnamed: J3.4, U3.4 (A01)

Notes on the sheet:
PWM pin is usually not used in this application and is always 1
Motor Driver 2
Power
Interfaces
Motor Driver 1
Motor Driver 3
Mechanical
Populate one of these diodes.
Micro Controller

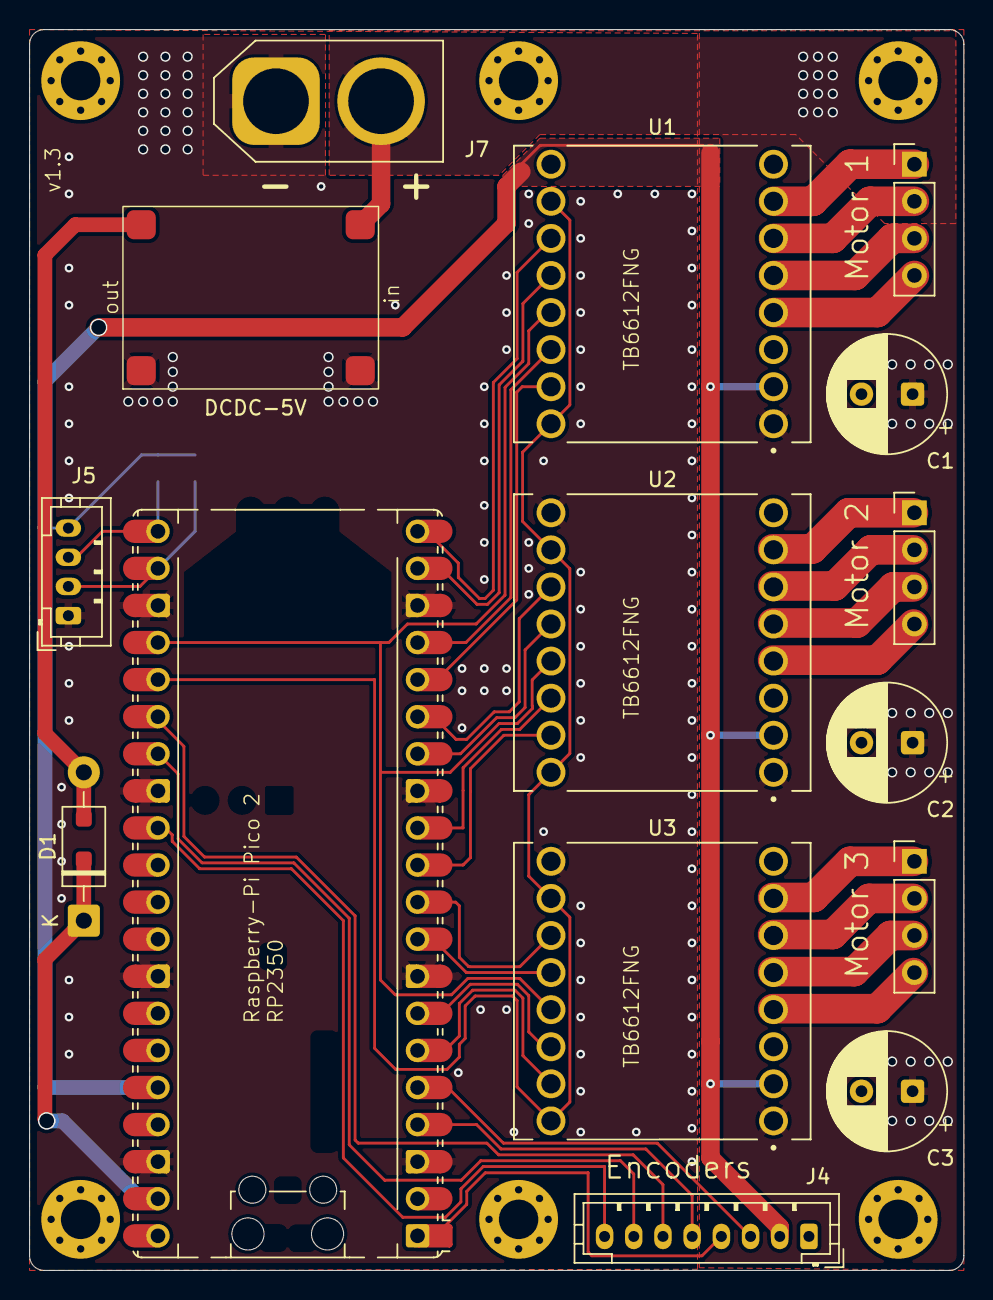
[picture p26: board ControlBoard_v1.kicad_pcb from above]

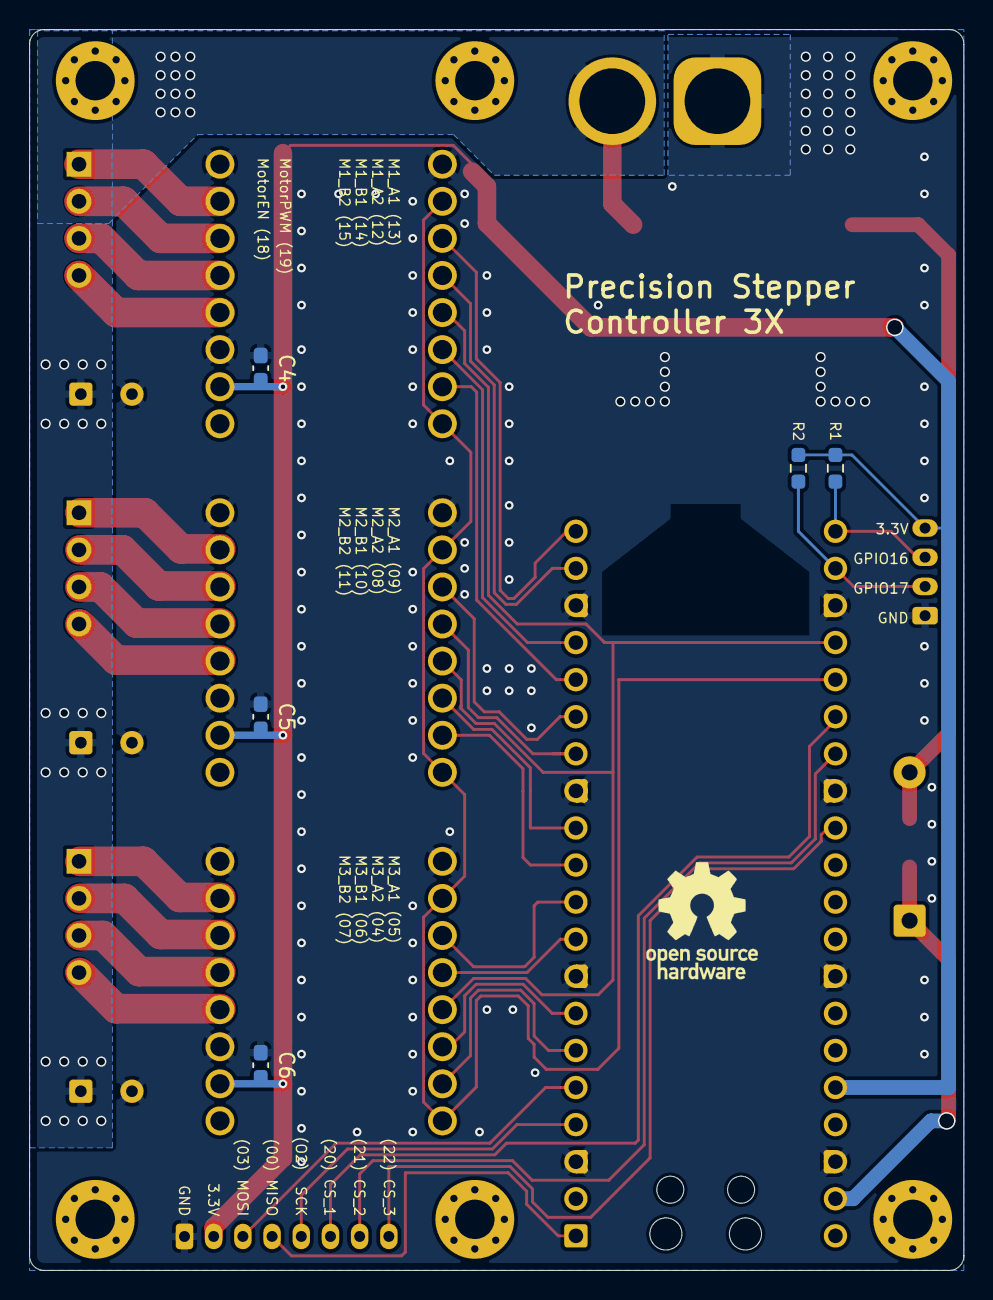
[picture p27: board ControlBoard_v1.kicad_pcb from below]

Board: 2 copper layers, 64.0 x 85.0 mm, 27 parts (6 on the bottom side), 39 nets.

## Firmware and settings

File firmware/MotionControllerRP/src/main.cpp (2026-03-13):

// --------------------------------------------------------------------------------------
// Project: MicroManipulatorStepper
// License: MIT (see LICENSE file for full description)
//          All text in here must be included in any redistribution.
// Author:  M. S. (diffraction limited)
// --------------------------------------------------------------------------------------

#include "main.h"

#include "hardware/clocks.h"
#include "hardware/pll.h"
#include "hardware/vreg.h"

#include <Wire.h>
#include <algorithm>

#include "robot.h"
#include "utilities/logging.h"
#include "utilities/frequency_counter.h"
#include "kinematic_models/kinematic_model_delta3d.h"
#include "version.h"
#include "hw_config.h"
#include "LittleFS.h"

#include "demo_gcode_generator.h"

//*** GLOBALS ***************************************************************************

// NeoPixelConnect strip(PIN_BUILTIN_LED, 1);
Robot robot(0.01f);

/*
MT6835Encoder encoder1(spi0, PIN_ENCODER1_CS);
MT6835Encoder encoder2(spi0, PIN_ENCODER2_CS);
MT6835Encoder encoder3(spi0, PIN_ENCODER3_CS);

TB6612MotorDriver motor_driver1(
  PIN_MOTOR_EN, PIN_M1_PWM_A_POS, PIN_M1_PWM_A_NEG, PIN_MOTOR_PWMAB,
  PIN_MOTOR_EN, PIN_M1_PWM_B_POS, PIN_M1_PWM_B_NEG, PIN_MOTOR_PWMAB
);
TB6612MotorDriver motor_driver2(
  PIN_MOTOR_EN, PIN_M2_PWM_A_POS, PIN_M2_PWM_A_NEG, PIN_MOTOR_PWMAB,
  PIN_MOTOR_EN, PIN_M2_PWM_B_POS, PIN_M2_PWM_B_NEG, PIN_MOTOR_PWMAB
);
TB6612MotorDriver motor_driver3(
  PIN_MOTOR_EN, PIN_M3_PWM_A_POS, PIN_M3_PWM_A_NEG, PIN_MOTOR_PWMAB,
  PIN_MOTOR_EN, PIN_M3_PWM_B_POS, PIN_M3_PWM_B_NEG, PIN_MOTOR_PWMAB
);

ServoController servo_controller1(motor_driver1, encoder1, 400/4);
ServoController servo_controller2(motor_driver2, encoder2, 400/4);
ServoController servo_controller3(motor_driver3, encoder3, 400/4);
FrequencyCounter loop_freq_counter(1000);

PathPlanner planner(0.01f);
MotionController motion_controller(&planner);
Pose6DF current_pose;

CommandParser command_parser; */

//*** FUNCTIONS *************************************************************************

// Run before setup()
//__attribute__((constructor))
void overclock() {
  vreg_set_voltage(VREG_VOLTAGE_1_20);         // For >133 MHz
  busy_wait_us(10 * 1000);  // 10 ms delay
  set_sys_clock_khz(250000, true);             // Set to 250 MHz
}

void set_led_color(uint8_t r, uint8_t g, uint8_t b) {
 /* strip.neoPixelSetValue(0, r, g, b, false);
  delayMicroseconds(2000);
  strip.neoPixelShow(); */
}

void led_blink(uint8_t r, uint8_t g, uint8_t b, int count, int period_time_ms) {
  for(int i=0; i<count; i++) {
    gpio_put(PIN_BUILTIN_LED, 1);
    // set_led_color(r, g, b);
    sleep_ms(period_time_ms/2);
    // set_led_color(0, 0, 0);
    gpio_put(PIN_BUILTIN_LED, 0);
    sleep_ms(period_time_ms/2);
  }
}

void main_core0() {
  uint64_t last_time = time_us_64();

  #ifdef DEMO_MODE
    auto* demo_gcode_generator = new DemoGcodeGenerator(&robot);
    demo_gcode_generator->run();  // blocks forever
  #endif

  while(true) {
    // update motion controller
    robot.update_command_parser();
    robot.update_path_planner();
  }
}

void main_core1() {
  LOG_INFO("Starting servo controll loops on core 1...");

  uint64_t last_time = time_us_64();
  while(true) {
    // get time and detla time
    uint64_t time_us = time_us_64();
    float dt = float(time_us - last_time)*1e-6f;
    last_time = time_us;

    // limit time delta
    dt = std::min(dt, 0.0001f);

    // update servo loops
    robot.update_servo_controllers(dt);
  }
}

void setup() {
  gpio_init(PIN_BUILTIN_LED);
  gpio_set_dir(PIN_BUILTIN_LED, GPIO_OUT);
  
  led_blink(0, 0, 30, 3, 100);
  // stdio_init_all();  // Initializes USB or UART stdio
  overclock();
  // Serial.begin(921600);
  Logger::instance().begin(921600, false);
  #ifndef DEMO_MODE
  while(!Serial);
  #endif

  set_led_color(50, 10, 0);
  // auto* test = new KinematicModel_Delta3D(); test->test(); delete test;

  delay(100);  // Allow time for serial monitor to connect
  
  LOG_INFO("Open Micro Stage Firmware: %s", FIRMWARE_VERSION);
  LOG_INFO("System clock: %i Mhz", int32_t(clock_get_hz(clk_sys))/1000/1000);

  // LittleFS.format();
  if (!LittleFS.begin()) {
    LOG_ERROR("Mounting filesystem failed");
  } else {
    FSInfo fs_info;
    LittleFS.info(fs_info);
    LOG_INFO("Mounting filesystem successfully [%i/%i bytes used]", 
             (int)fs_info.usedBytes, (int)fs_info.totalBytes);
  }

  LOG_INFO("Initializing device...");
  robot.init();

  multicore_launch_core1(&main_core1);
  sleep_ms(100);
  
  set_led_color(0, 20, 0);
  LOG_INFO("Initialization finished");
  LOG_INFO(" ");

  gpio_put(PIN_BUILTIN_LED, 1);

  return;

  /*
  rotencoder_wire.setSDA(PIN_ENCODER_SDA);
  rotencoder_wire.setSCL(PIN_ENCODER_SCL);
  rotencoder_wire.begin();
  rotencoder_wire.setClock(1000000);
  encoder.init();
  encoder.set_hysteresis(0x4); //0x6);
  */
}

void loop() {
  main_core0();
}

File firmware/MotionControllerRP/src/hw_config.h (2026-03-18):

#pragma once
#include "utilities/math_constants.h"

// #define DEMO_MODE

//--- MOTORS ------------------------------------------------------------------

// motor pole pair count
//  * 100 for 0.9deg stepper motors
//  * 50  for 1.8deg stepper motors
constexpr float MOTOR1_POLE_PAIRS = 50;
constexpr float MOTOR2_POLE_PAIRS = 50;
constexpr float MOTOR3_POLE_PAIRS = 50;

// max current factor in range [0..1]. Lower values reduce pwm resolution so a
// value above 0.4 is recommended.
constexpr float MOTOR_MAX_CURRENT_FACTOR = 0.6f;

//--- ENCODERS ----------------------------------------------------------------

// Conversion factor from encoder angle (one 2pi period every two magnets) to rotor angle.
// Used when the system can not rely on calibration data being present (e.g. during homing)
constexpr float ENCODER_MAGNET_PITCH = 3.0f;    // [mm]
constexpr float ENCODER_MAGNET_RADIUS = 30.0f;  // [mm]
constexpr float ENCODER_ANGLE_TO_ROTOR_ANGLE = (ENCODER_MAGNET_PITCH*2.0f) / 
                                               (ENCODER_MAGNET_RADIUS * Constants::TWO_PI_F);
											   
// enables error checking for encoders (slow) - useful for debugging
// Note: some chips seem to return always a crc of 0 producing massiv false errors       
constexpr bool ENABLE_ENCODER_CRC = false;

//--- HOMING ------------------------------------------------------------------

constexpr float HOMING_VELOCITY   = 1.0f;        // rad per s
constexpr float HOMING_CURRENT    = 0.15f;       // range 0..1
// NOT IMPLEMENTED YET: constexpr float HOMING_FINISH_POS = 0.5f;        // in rad

//--- CALIBRATION -------------------------------------------------------------

// degrees from home position
constexpr float CALIBRATION_RANGE = 83; 

// velocity of the magnetic field during calibration (lower is more accurate)
constexpr float CALIBRATION_FIELD_VELOCITY = 20.0f; 

// size of the calibration lookup table
constexpr int ENCODER_LUT_SIZE = 256;

//--- CLOSED LOOP CONTROL -----------------------------------------------------

// position controller 
constexpr float POS_KP = 60.0f;
constexpr float POS_KI = 30000.0f;

// velocity controller
constexpr float VEL_LOWPASS_TC = 0.004f;
constexpr float VEL_KP = 0.2f;
constexpr float VEL_KI = 90.0f;

//--- KINEMATIC ---------------------------------------------------------------

// Kinematic Parameters are defined kinematic_modes/kinematic_model_delta3d.cpp

// NUM_JOINTS and NUM_TOOLS are defined in 'path_segment.h'. Note that changing
// the number of joints requires changing the kinematic model accordingly and
// also requires the initialization of the correct number of 'RobotJoint' objects
// in the Robtos init method.

//--- PINS --------------------------------------------------------------------

#define JOINT_READY_OVERRIDE

// #define SINGLE_AXIS_BOARD
#ifndef SINGLE_AXIS_BOARD
  // Pins for 3Axis Board
  // #define PIN_BUILTIN_LED 23 // RP2040 pico clone
  // #define PIN_USER_BUTTON 24 // RP2040 pico clone
  #define PIN_BUILTIN_LED 25

  #define PIN_M1_PWM_A_POS  13
  #define PIN_M1_PWM_A_NEG  12
  #define PIN_M1_PWM_B_POS  14
  #define PIN_M1_PWM_B_NEG  15

  #define PIN_M2_PWM_A_POS  9
  #define PIN_M2_PWM_A_NEG  8
  #define PIN_M2_PWM_B_POS  10
  #define PIN_M2_PWM_B_NEG  11

  #define PIN_M3_PWM_A_POS  5
  #define PIN_M3_PWM_A_NEG  4
  #define PIN_M3_PWM_B_POS  6
  #define PIN_M3_PWM_B_NEG  7


  #define PIN_MOTOR_EN      18
  #define PIN_MOTOR_PWMAB   19

  #define PIN_ENCODER1_CS 20
  #define PIN_ENCODER2_CS 21
  #define PIN_ENCODER3_CS 22
  #define PIN_ENCODER_SCK 2
  #define PIN_ENCODER_MISO 0
  #define PIN_ENCODER_MOSI 3

  #define PIN_TOOL1 16
  #define PIN_TOOL2 17

#else
  // Single Axis Board
  #define PIN_BUILTIN_LED 16
  #define PIN_USER_BUTTON 24

  #define PIN_M1_PWM_A_POS  13
  #define PIN_M1_PWM_A_NEG  12
  #define PIN_M1_PWM_B_POS  14
  #define PIN_M1_PWM_B_NEG  15

  #define PIN_M2_PWM_A_POS  9
  #define PIN_M2_PWM_A_NEG  8
  #define PIN_M2_PWM_B_POS  10
  #define PIN_M2_PWM_B_NEG  11

  #define PIN_M3_PWM_A_POS  5
  #define PIN_M3_PWM_A_NEG  4
  #define PIN_M3_PWM_B_POS  6
  #define PIN_M3_PWM_B_NEG  7


  #define PIN_MOTOR_EN      18
  #define PIN_MOTOR_PWMAB   19

  #define PIN_ENCODER1_CS 20
  #define PIN_ENCODER2_CS 21
  #define PIN_ENCODER3_CS 22
  #define PIN_ENCODER_SCK 2
  #define PIN_ENCODER_MISO 0
  #define PIN_ENCODER_MOSI 3
#endif

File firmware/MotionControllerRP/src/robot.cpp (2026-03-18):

// --------------------------------------------------------------------------------------
// Project: MicroManipulatorStepper
// License: MIT (see LICENSE file for full description)
//          All text in here must be included in any redistribution.
// Author:  M. S. (diffraction limited)
// --------------------------------------------------------------------------------------

#include <LittleFS.h> 
#include "robot.h"
#include "hw_config.h"
#include "utilities/logging.h"
#include "utilities/utilities.h"
#include "kinematic_models/kinematic_model_delta3d.h"
#include "servo_control/homing_controller.h"
#include "servo_control/actuator_calibration.h"
#include "robot_joint/robot_joint.h"
#include "pico/multicore.h"
#include "version.h"
#include "robot_tool/pwm_tool.h"

constexpr int SPINLOCK_ID_SHARED_DATA = 0;
constexpr int SPINLOCK_ID_JOINTS = 1;

#include <NeoPixelConnect.h>
NeoPixelConnect led(PIN_BUILTIN_LED, 1);

//*** FUNCTION **************************************************************************

bool startswith(const std::string& str, const std::string& prefix) {
    return str.size() >= prefix.size() &&
           std::equal(prefix.begin(), prefix.end(), str.begin());
}

//*** CLASS *****************************************************************************

//--- Robot -----------------------------------------------------------------------------

Robot::Robot(float path_segment_time_step) : 
  path_planner(nullptr, path_segment_time_step), 
  motion_controller(&path_planner),
  servo_loop_frequency_counter(10000),
  motion_controller_frequency_counter(1000),
  shared_data(SPINLOCK_ID_SHARED_DATA),
  joints_spin_lock(spin_lock_instance(SPINLOCK_ID_JOINTS))
{
  kinematic_model = new KinematicModel_Delta3D();
  path_planner.set_kinematic_model(kinematic_model);

  for(int i=0; i<NUM_JOINTS; i++)
    joints[i] = nullptr;

  command_parser.set_command_processor(this);

  current_feedrate = LinearAngular(10.0f, 1.0f);
  max_acceleration = LinearAngular(500.0f, 50.0f);
  path_buffering_time_us = 50*1e3;

  for(int i=0; i<NUM_TOOLS; i++)
    robot_tools[i] = nullptr;

  state = ERobotState::IDLE;
}

Robot::~Robot() {
  if(kinematic_model != nullptr)
    delete kinematic_model;

  for(int i=0; i<NUM_JOINTS; i++) {
    if(joints[i] != nullptr)
      delete joints[i];
    joints[i] = nullptr;
  }
}

void Robot::init() {
  MT6835Encoder::setup_spi(spi0, PIN_ENCODER_SCK, PIN_ENCODER_MOSI, PIN_ENCODER_MISO, 8000000);

  // axis 1
  {
    auto* encoder = new MT6835Encoder(spi0, PIN_ENCODER1_CS);
    auto* motor_driver = new TB6612MotorDriver(
      PIN_MOTOR_EN, PIN_M1_PWM_A_POS, PIN_M1_PWM_A_NEG, PIN_MOTOR_PWMAB,
      PIN_MOTOR_EN, PIN_M1_PWM_B_POS, PIN_M1_PWM_B_NEG, PIN_MOTOR_PWMAB
    );
	encoder->set_crc_enabled(ENABLE_ENCODER_CRC);
    joints[0] = new RobotJoint(encoder, motor_driver, MOTOR1_POLE_PAIRS);
  }

  // axis 2
  {
    auto* encoder = new MT6835Encoder(spi0, PIN_ENCODER2_CS);
    auto* motor_driver = new TB6612MotorDriver(
      PIN_MOTOR_EN, PIN_M2_PWM_A_POS, PIN_M2_PWM_A_NEG, PIN_MOTOR_PWMAB,
      PIN_MOTOR_EN, PIN_M2_PWM_B_POS, PIN_M2_PWM_B_NEG, PIN_MOTOR_PWMAB
    );
	encoder->set_crc_enabled(ENABLE_ENCODER_CRC);
    joints[1] = new RobotJoint(encoder, motor_driver, MOTOR2_POLE_PAIRS);
  }

  // axis 3
  {
    auto* encoder = new MT6835Encoder(spi0, PIN_ENCODER3_CS);
    auto* motor_driver = new TB6612MotorDriver(
      PIN_MOTOR_EN, PIN_M3_PWM_A_POS, PIN_M3_PWM_A_NEG, PIN_MOTOR_PWMAB,
      PIN_MOTOR_EN, PIN_M3_PWM_B_POS, PIN_M3_PWM_B_NEG, PIN_MOTOR_PWMAB
    );
	encoder->set_crc_enabled(ENABLE_ENCODER_CRC);
    joints[2] = new RobotJoint(encoder, motor_driver, MOTOR3_POLE_PAIRS);
  }

  // initialize axes
  for(int i=0; i<NUM_JOINTS; i++) {
    joints[i]->init(i);
    joints[i]->load_calibration();
  }

  // add tools
  robot_tools[0] = new PwmTool();
  ((PwmTool*)robot_tools[0])->init(PIN_TOOL1, 8000, 8);

  robot_tools[1] = new PwmTool();
  ((PwmTool*)robot_tools[1])->init(PIN_TOOL2, 8000, 8);

  // setup timer for updating the motion controller (which evaluates joint space path
  // segments and produces the current target position for the servo loops)
  float motion_controller_update_time_us = 500;
  add_repeating_timer_us(-motion_controller_update_time_us, 
                         Robot::update_motion_controller_isr, 
                         (void*)this, 
                         &motion_controller_update_timer);
}


void Robot::update_command_parser() {
  // process serial input
  if (Serial.available()) {
    char c = Serial.read();
    command_parser.add_input_character(c);
    // Serial.write(c);
  }

  // update command parse which will queue command to the path planner
  command_parser.update();

  // TESTING:
  //sleep_ms(10);
  //float pos_error = joints[1]->servo_controller->get_position_error();
  //LOG_INFO(">pos_error [µrad]: %f\n", pos_error*1e6);
  //Serial.printf(">pos_error [µrad]: %f\n", pos_error*1e6);#
  //LOG_INFO(">pos_x [mm]: %f", joints[1]->position);
  //update_servo_controllers(0.01f);
}

/**
 * Updates the path planner, that chops up kartesian path segments into joint space
 * path segments using the inverse kinematic model. It then enqueues these joint space path
 * segments for the motion controller.
 */
void Robot::update_path_planner() {
  // check if buffering starts
  uint64_t time = time_us_64();
  if(state == ERobotState::IDLE && path_planner.input_queue_size() > 0) {
    state = ERobotState::BUFFERING_PATH;
    path_buffering_start_time = time;
  }

  // check if execution starts
  uint64_t buffering_time = time-path_buffering_start_time;
  if(state == ERobotState::BUFFERING_PATH && buffering_time > path_buffering_time_us) {
    state = ERobotState::EXECUTING_PATH;
  }

  // execute path
  if(state == ERobotState::EXECUTING_PATH) {
    // update planner and generate joint space path segments
    path_planner.process(true);

    if(path_planner.all_finished())
      state = ERobotState::IDLE;
  }
}
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

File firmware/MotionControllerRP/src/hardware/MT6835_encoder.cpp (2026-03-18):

// --------------------------------------------------------------------------------------
// This code is a modified version of the MT6835 Driver from the SimpleFOC project
// being distributed under the MIT liscence as well. Thank you SimpleFOC !
// --------------------------------------------------------------------------------------

#include "MT6835_encoder.h"
#include "hardware/spi.h"
#include "hardware/gpio.h"
#include "pico/stdlib.h"
#include "utilities/logging.h"

void MT6835Encoder::setup_spi(spi_inst_t* spi, uint pin_sck, uint pin_mosi, uint pin_miso, int32_t baudrate_hz) {
  // Set GPIO functions to SPI
  gpio_set_function(pin_sck, GPIO_FUNC_SPI);
  gpio_set_function(pin_mosi, GPIO_FUNC_SPI);
  gpio_set_function(pin_miso, GPIO_FUNC_SPI);
  
  // SPI format: 8 bits, mode 3 (CPOL=1, CPHA=1)
  spi_init(spi, baudrate_hz);
  spi_set_format(spi, 8, SPI_CPOL_1, SPI_CPHA_1, SPI_MSB_FIRST);

  sleep_ms(10);
}

MT6835Encoder::MT6835Encoder(spi_inst_t* spi, int32_t cs_pin) : spi(spi), cs_pin(cs_pin) {
  if (cs_pin >= 0) {
      gpio_init(cs_pin);
      gpio_set_dir(cs_pin, GPIO_OUT);
      gpio_put(cs_pin, 1);  // CS high
  }
}

MT6835Encoder::~MT6835Encoder() {
  // nop
}

bool MT6835Encoder::init(uint8_t bandwidth, uint8_t hysteresis) {
  sleep_ms(100);

  if(is_connected() == false)
    return false;

  set_rotation_direction(0);    // needs to be set, otherwise might be random
  set_bandwidth(bandwidth);
  set_hysteresis(hysteresis);

  last_raw_angle = 0;
  abs_raw_angle = 0;
  crc_error_count = 0;
  initialized = true;

  return true;
}

bool MT6835Encoder::is_connected() {
  uint8_t check_bytes[] = {37, 109, 179, 251, 1};
  for(int i=0; i<sizeof(check_bytes); i++) {
    write_register(MT6835_REG_USERID, check_bytes[i]);
    uint8_t user_id = read_register(MT6835_REG_USERID);
    if(user_id != check_bytes[i])
      return false;
  }

  return true;
}

bool MT6835Encoder::is_initialized() {
  return initialized;
}

void MT6835Encoder::reset_abs_angle(int32_t abs_raw_angle) {
  MT6835Encoder::abs_raw_angle = abs_raw_angle;
}

void MT6835Encoder::reset_abs_angle_period() {
  abs_raw_angle %= MT6835_CPR;
  if (abs_raw_angle < 0)
    abs_raw_angle += MT6835_CPR;
}

float MT6835Encoder::read_abs_angle() {
  int32_t raw_angle = read_abs_angle_raw();
  return raw_angle * RAW_TO_ANGLE;
}

MT6835Encoder::AbsRawAngleType MT6835Encoder::read_abs_angle_raw() {
  uint8_t data[6] = {0};
  data[0] = MT6835_OP_ANGLE << 4;
  data[1] = MT6835_REG_ANGLE1;
  // rest zero

  spi_begin_transaction();
  spi_transfer(data, 6);
  spi_end_transaction();

  last_status = data[4] & 0x07;
  last_crc = data[5];
  int32_t raw_angle = ((int32_t)data[2] << 13) | ((int32_t)data[3] << 5) | (data[4] >> 3);
  
  if (check_crc) {
      if (last_crc != calc_crc(raw_angle, last_status)) {
          last_status |= MT6835_CRC_ERROR;
          crc_error_count++;
          // LOG_ERROR("chip_crc: %i - calc_crc: %i", last_crc, calc_crc(raw_angle, last_status));
     //     return -1.0f; // CRC error indicator
      }
  }

  return update_abs_raw_angle(raw_angle);
}

MT6835Encoder::AbsRawAngleType MT6835Encoder::get_last_abs_raw_angle() const {
  return abs_raw_angle;
}

float MT6835Encoder::get_last_abs_angle() const {
  return abs_raw_angle * RAW_TO_ANGLE;
}

int32_t MT6835Encoder::get_rawcounts_per_rev() {
  return MT6835_CPR;
}

uint8_t MT6835Encoder::get_status() {
    return last_status;
}

void MT6835Encoder::set_crc_enabled(bool enable) {
  check_crc = enable;
}

bool MT6835Encoder::is_crc_enabled() {
  return check_crc;
}

uint32_t MT6835Encoder::get_crc_error_count(bool reset) {
  uint32_t result = crc_error_count;
  if(reset)
    crc_error_count = 0;
  return result;
}

uint8_t MT6835Encoder::get_calibration_status() {
    uint8_t data[3] = {0};
    data[0] = (MT6835_OP_READ << 4) | (MT6835_REG_CAL_STATUS >> 8);
    data[1] = MT6835_REG_CAL_STATUS & 0xFF;

    spi_begin_transaction();
    spi_transfer(data, 3);
    spi_end_transaction();

    return data[2] >> 6;
}

bool MT6835Encoder::set_zero_from_current_position() {
    MT6835Command cmd{};
    cmd.cmd = MT6835_OP_ZERO;
    cmd.addr = 0x000;
    transfer_24(&cmd);
    abs_raw_angle = 0;
    last_raw_angle = 0;
    return cmd.data == MT6835_WRITE_ACK;
}

bool MT6835Encoder::write_eeprom() {
    sleep_ms(1); // wait at least 1 ms
    MT6835Command cmd{};
    cmd.cmd = MT6835_OP_PROG;
    cmd.addr = 0x000;
    transfer_24(&cmd);
    return cmd.data == MT6835_WRITE_ACK;
}

uint8_t MT6835Encoder::get_bandwidth() {
    MT6835Options5 opts{ .reg = read_register(MT6835_REG_OPTS5) };
    return opts.bw;
}
void MT6835Encoder::set_bandwidth(uint8_t bw) {
    MT6835Options5 opts{ .reg = read_register(MT6835_REG_OPTS5) };
    opts.bw = bw;
    write_register(MT6835_REG_OPTS5, opts.reg);
}

uint8_t MT6835Encoder::get_hysteresis() {
    MT6835Options3 opts{ .reg = get_options3().reg };
    return opts.hyst;
}
void MT6835Encoder::set_hysteresis(uint8_t hyst) {
    MT6835Options3 opts{ .reg = get_options3().reg };
    opts.hyst = hyst;
    set_options3(opts);
}

uint8_t MT6835Encoder::get_rotation_direction() {
    MT6835Options3 opts{ .reg = get_options3().reg };
    return opts.rot_dir;
}
void MT6835Encoder::set_rotation_direction(uint8_t dir) {
    MT6835Options3 opts{ .reg = get_options3().reg };
    opts.rot_dir = dir;
    set_options3(opts);
}

uint16_t MT6835Encoder::get_abz_resolution() {
    uint8_t hi = read_register(MT6835_REG_ABZ_RES1);
    MT6835ABZRes lo{ .reg = read_register(MT6835_REG_ABZ_RES2) };
    return (hi << 6) | lo.abz_res_low;
}
void MT6835Encoder::set_abz_resolution(uint16_t res) {
    uint8_t hi = (res >> 6);
    MT6835ABZRes lo{ .reg = read_register(MT6835_REG_ABZ_RES2) };
    lo.abz_res_low = (res & 0x3F);
    write_register(MT6835_REG_ABZ_RES1, hi);
    write_register(MT6835_REG_ABZ_RES2, lo.reg);
}

bool MT6835Encoder::is_abz_enabled() {
    MT6835ABZRes lo{ .reg = read_register(MT6835_REG_ABZ_RES2) };
    return lo.abz_off == 0;
}
void MT6835Encoder::set_abz_enabled(bool enabled) {
    MT6835ABZRes lo{ .reg = read_register(MT6835_REG_ABZ_RES2) };
    lo.abz_off = enabled ? 0 : 1;
    write_register(MT6835_REG_ABZ_RES2, lo.reg);
}

bool MT6835Encoder::is_ab_swapped() {
    MT6835ABZRes lo{ .reg = read_register(MT6835_REG_ABZ_RES2) };
    return lo.ab_swap == 1;
}
void MT6835Encoder::set_ab_swapped(bool swapped) {
    MT6835ABZRes lo{ .reg = read_register(MT6835_REG_ABZ_RES2) };
    lo.ab_swap = swapped ? 1 : 0;
    write_register(MT6835_REG_ABZ_RES2, lo.reg);
}

uint16_t MT6835Encoder::get_zero_position() {
    uint8_t hi = read_register(MT6835_REG_ZERO1);
    MT6835Options0 lo{ .reg = read_register(MT6835_REG_ZERO2) };
    return (hi << 4) | lo.zero_pos_low;
}
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

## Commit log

2025-12-02 add a PCB to distribute the SPI bus to multiple encoders
    [EncoderBoard.kicad_pcb, EncoderBoard.kicad_sch]
2026-01-03 Update magnets size and grade in bom.md for more relyable encoder readings
2026-02-22 added CAD files for HW version 4
    [Assembly_Actuator.FCStd, Assembly_BallJointPlate.FCStd, Assembly_EndEffector.FCStd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]
2026-02-25 added production files added subfolders in electroncs
    [ControlBoard_v1.kicad_pcb, ControlBoard_v1.kicad_sch]
2026-02-25 added pcb production files
    [designators.csv]
2026-02-25 updated CAD Image
2026-03-18 added optional CRC check for debugging Encoder SPI communication
2026-03-19 homing dir image
2026-03-24 added .stls from v4
    [BaseBlock.stl, EndEffector.stl, MotorHorn.stl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]
2026-03-24 added tool .stl's and reorganized folders
    [BaseBlock.stl, BladeCarrier.stl, CaliperClamp.stl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]
2026-03-24 wip bom 3d print update, divided into machines and tools
2026-04-19 Update Neodym Cylinder Magnet link in BOM
    Updated the suggested link for Neodym Cylinder Magnet to a specific supplier.
